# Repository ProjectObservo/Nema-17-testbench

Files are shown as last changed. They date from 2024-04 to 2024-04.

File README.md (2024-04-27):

# Nema 17 test bench
Welcome to this NEMA 17 Stepper Motor Test Bench repository!

This 3D printable test bench offers precision, reliability, and efficiency for testing NEMA 17 stepper motors. This platform is designed to streamline your testing process, providing accurate results with ease. Whether you're fine-tuning performance or ensuring quality control.

Nema 17 bench

## 3D printing list

You can find all the printable files in the CAD directory.
Use 15 to 25% infill for good results.

| Name | Amount | Comment |
| --- | --- | --- |
| Nema 17 motor mount | 1 | - |
| Limit switch | 1 | - |
| Limit switch (Mirror) | 1 | - |
| Belt holder | 1 | 2mm is the default.<br /> Pick 2.5mm if the belt does not fit. |
| Belt holder (Mirror)  | 1 | 2mm is the default.<br /> Pick 2.5mm if the belt does not fit. |
| Carriage runner | 1 | - |
| Bearing cage | 2 | 11.05mm is the default.<br /> Pick 11.2mm if the bearing does not fit. |

When you still have trouble to print the belt holder or bearing cage try to change the print scale e.g to 100.1% (bigger) or 99.9% (smaller) to slightly change the dimensions. 

## Buy list

| Name | Amount | Comment |
| --- | --- | --- |
| MGN12H slider | 1 | Pick any length you want. (Image shows 400mm) |
| GT2 open belt | 1 | Length = (Slider length[mm] * 3) +  160 mm <br />(Belt in image is ~1360mm long) |
| GT2 T30 pulley | 2 | |
| GT2 T16 IDLE pulley | 2 | No teeth ! |
| Brass insert | 14 | M3 x 5 (outer diameter 5mm) |
| Micro switch | 2 | SS-5GL or similar |
| M3 x 10 bolt | 20 | For motor, MGN12H slider and all brass insert mounts. |
| M3 x 20 bolt | 2 | Idler pulley |
| Bearing 685 | 2 | |
| M5 x 50 theaded rod | 1 | used as an axle[^1] |
| M5 Nut | 2 | |

Assembled            |  Disassembled
:-------------------------:|:-------------------------:
 | 

Note that the Bearing cage should be facing outward so that the bearing is visable (on both sides) when using a threaded rod instead of a solid axle.

[^1]:A solid axle can also be used but requires a lathe to create a slot to lock it in place with C retainer clips.

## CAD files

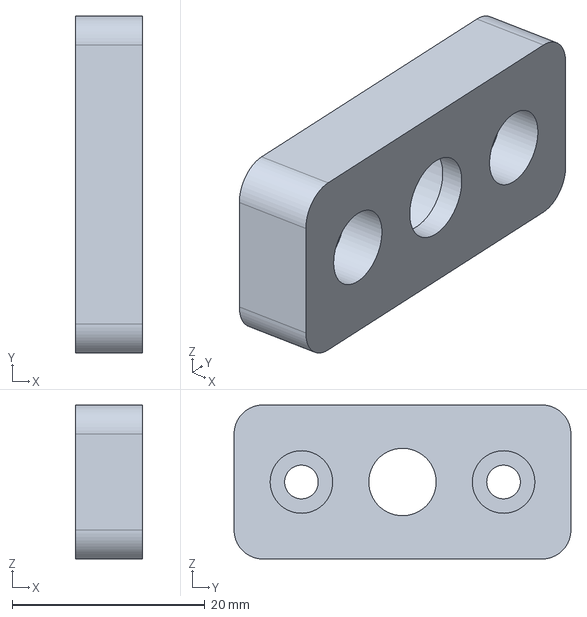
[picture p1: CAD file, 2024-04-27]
CAD/Bearing cage/Bearing cage 11.2 mm.step
7.00 x 35.0 x 16.0 mm

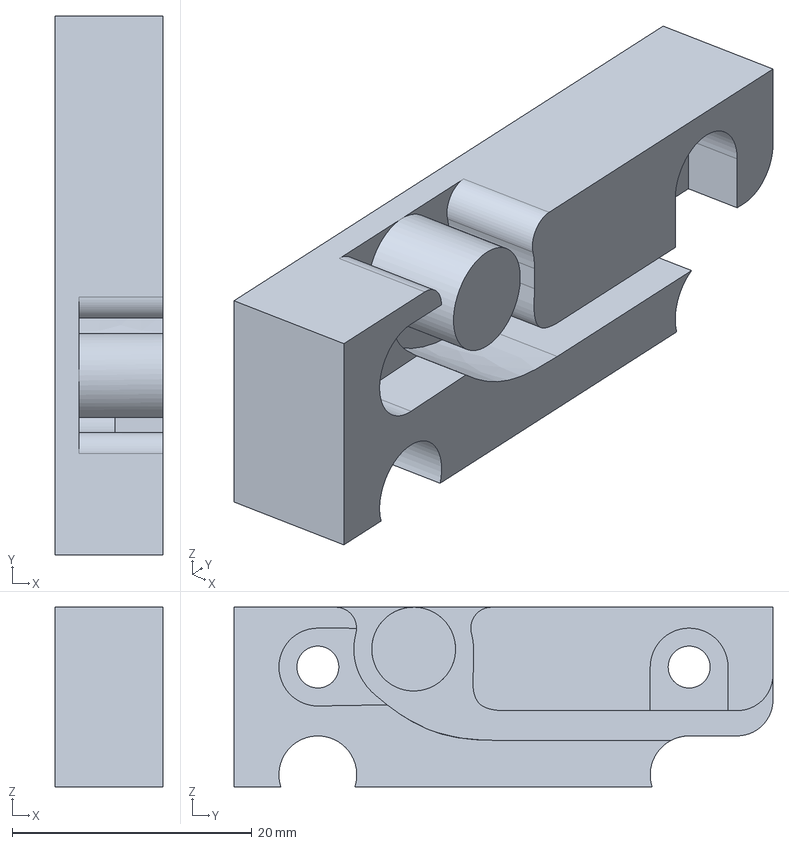
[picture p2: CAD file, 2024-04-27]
CAD/Belt holder loose (2.5 mm)/Belt Holder loose.step
9.00 x 45.0 x 15.0 mm

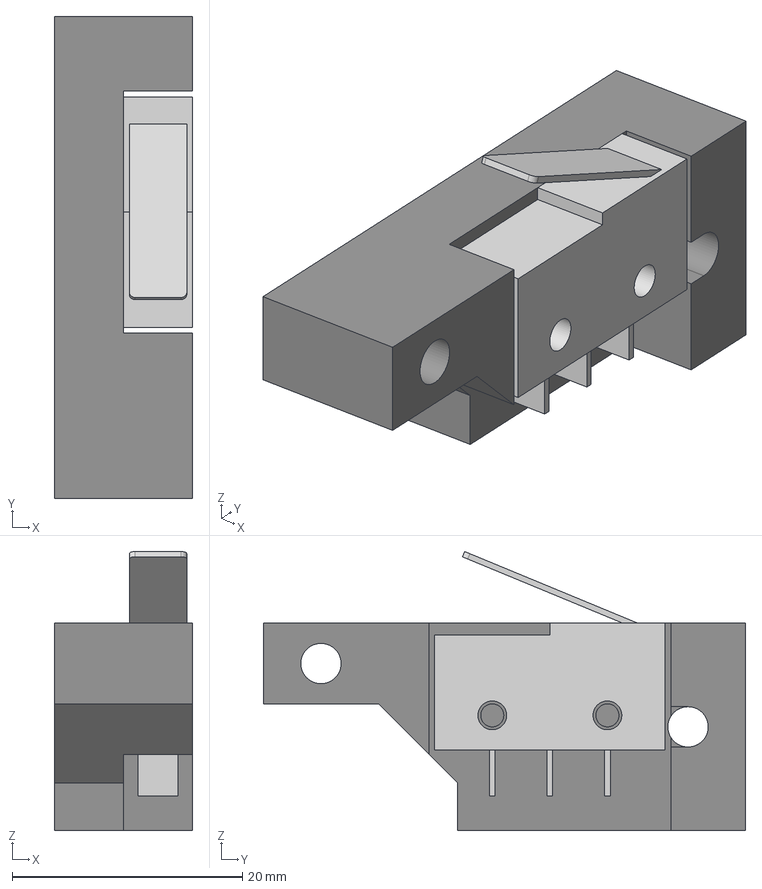
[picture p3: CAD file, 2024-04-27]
CAD/Limit switch.step
12.0 x 41.9 x 24.2 mm
pins
lever
Limit switch holder

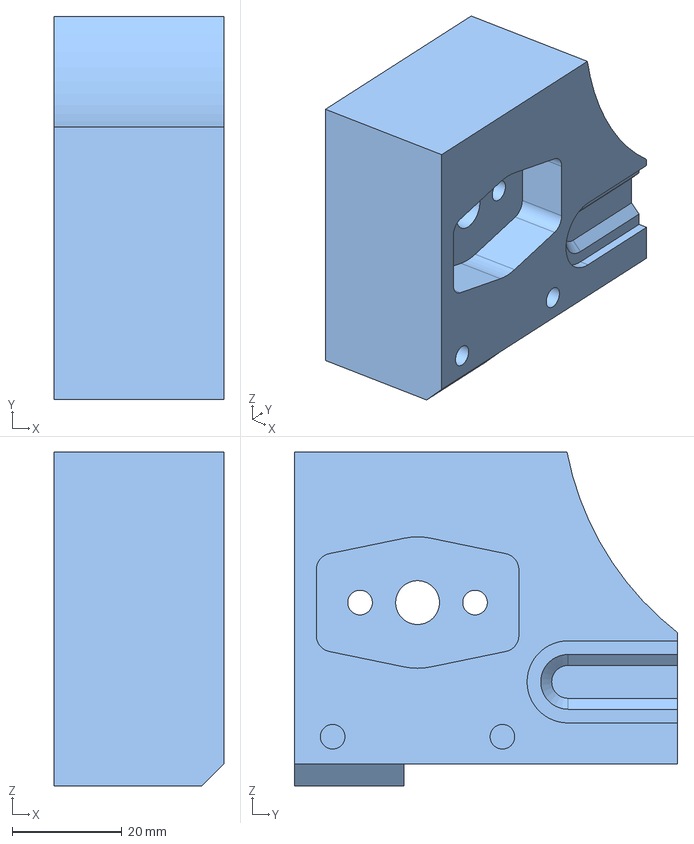
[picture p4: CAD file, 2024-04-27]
CAD/Idle pulley holder.step
31.0 x 70.0 x 61.0 mm

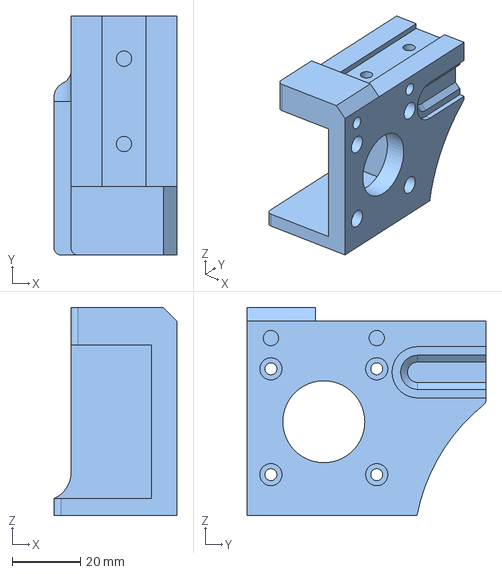
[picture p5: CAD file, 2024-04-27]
CAD/Nema 17 motor mount.step
36.0 x 70.0 x 61.0 mm

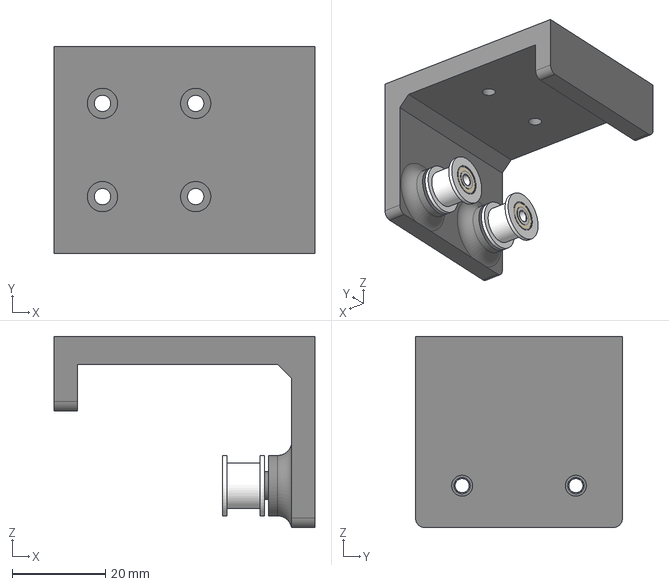
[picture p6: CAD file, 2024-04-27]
CAD/Carriage runner.step
56.0 x 44.4 x 41.0 mm
POWGE 2GT idler 16T B3 x 2

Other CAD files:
CAD/Belt holder tight (2.0 mm)/Belt Holder tight (Mirror).step
CAD/Bearing cage/Bearing cage 11.05 mm.step
CAD/Belt holder loose (2.5 mm)/Belt Holder loose (Mirror).step
CAD/Belt holder tight (2.0 mm)/Belt Holder tight.step
CAD/Limit switch(Mirror).step
